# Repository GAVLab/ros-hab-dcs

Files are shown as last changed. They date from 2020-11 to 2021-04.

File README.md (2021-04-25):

# ros-hab-dcs

Robot Operating System (ROS) High Altitude Balloon (HAB) Data Collection System (DCS)

**Status:** Launched maiden flight

## Introduction

This is a system to collect a high altitude balloon dataset utilizing ROS for aerial navigation algorithmic development.  The datasets contain downward facing visual imagery, side-facing imagery, IMU, GPS, external barometric pressure, and internal and external temperature.  The system is designed to run Ubuntu Mate 20.04LTS with ROS Noetic Ninjemys on a Raspberry Pi 4 and an Arduino Nano.

## Installation

Please see the installation guide for how to setup the software packages and run the system: [documentation/INSTALLATION.md](documentation/INSTALLATION.md)

## Photos
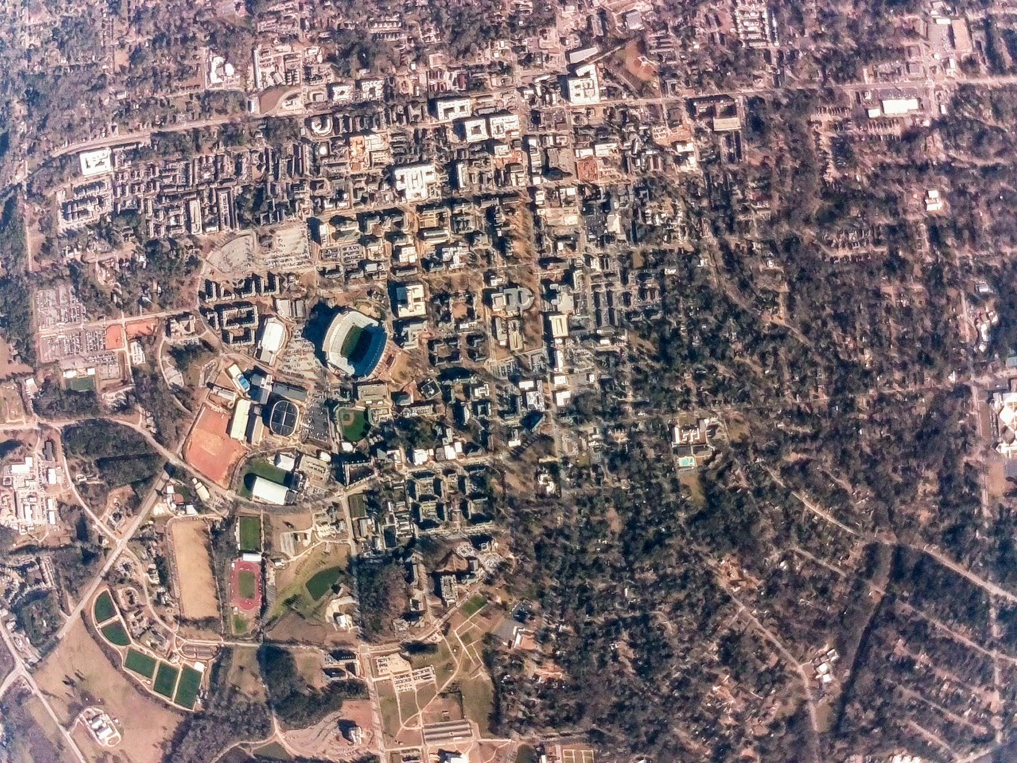
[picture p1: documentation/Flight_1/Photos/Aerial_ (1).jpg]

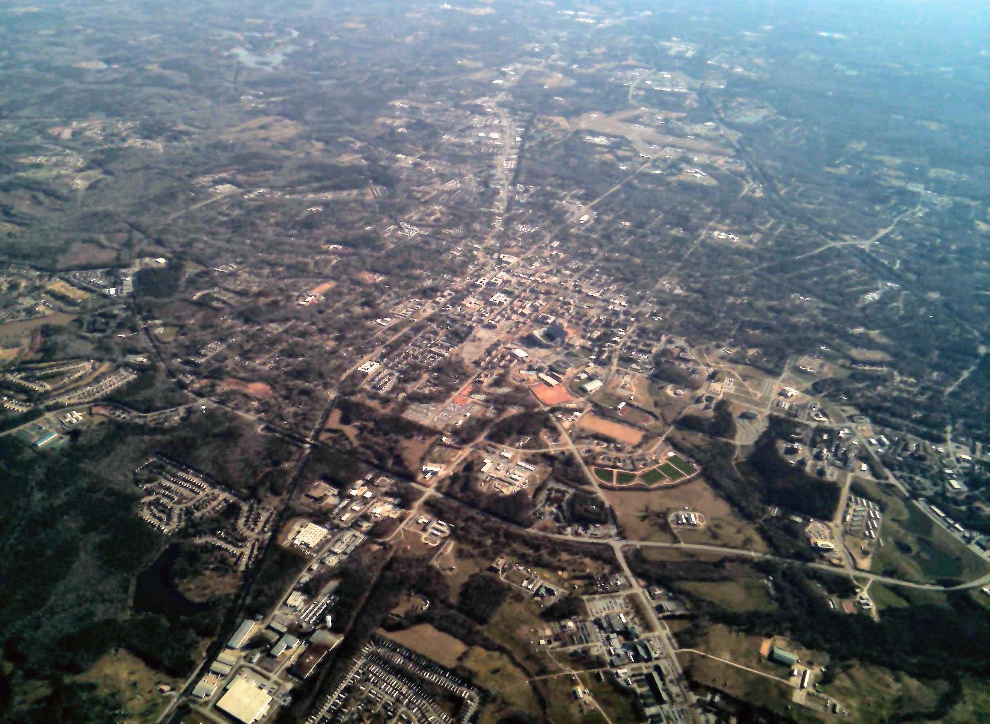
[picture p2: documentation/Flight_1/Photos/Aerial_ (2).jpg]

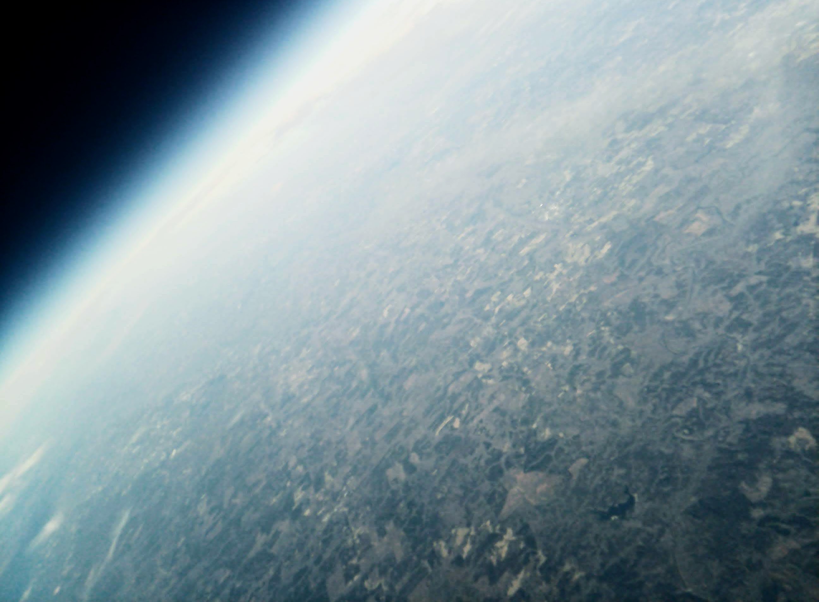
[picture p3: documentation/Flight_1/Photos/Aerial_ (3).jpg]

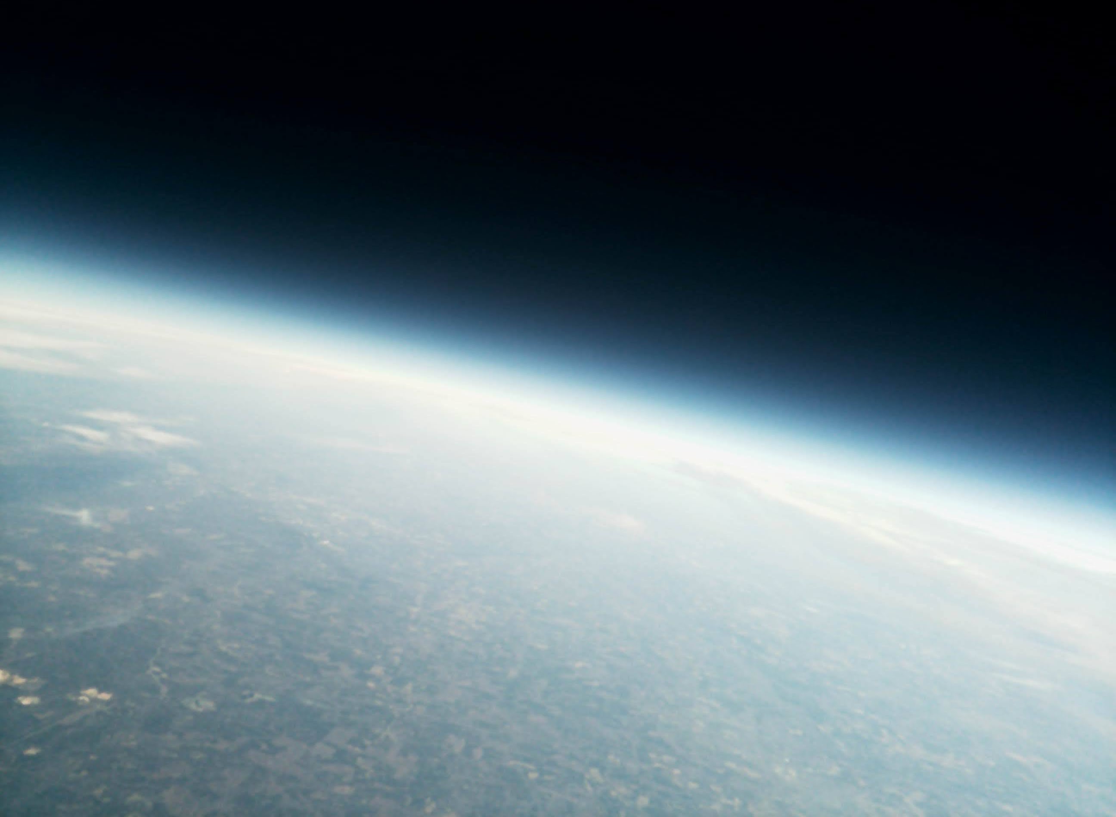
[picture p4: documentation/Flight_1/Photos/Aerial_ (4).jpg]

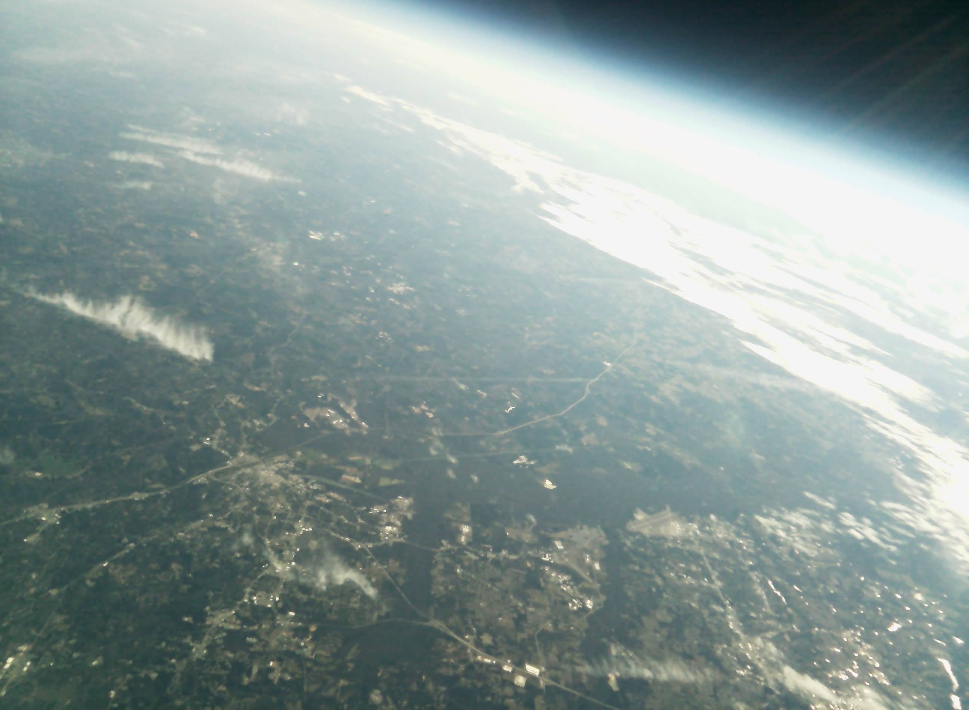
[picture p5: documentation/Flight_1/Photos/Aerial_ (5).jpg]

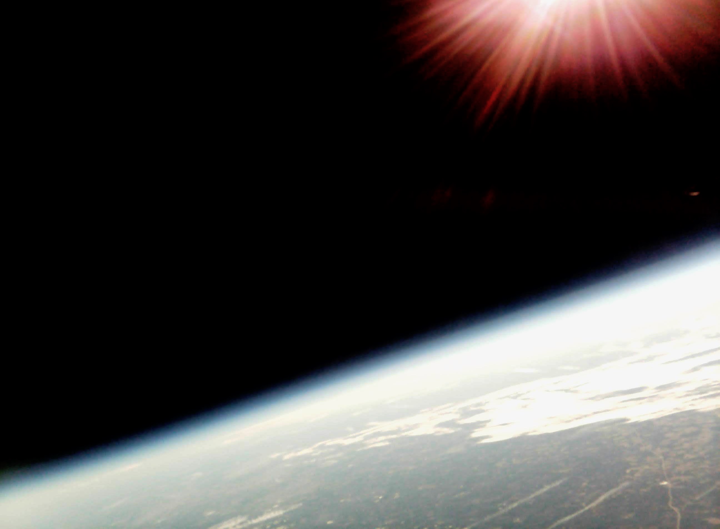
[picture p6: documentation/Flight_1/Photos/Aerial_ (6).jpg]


## Hardware

* SN01

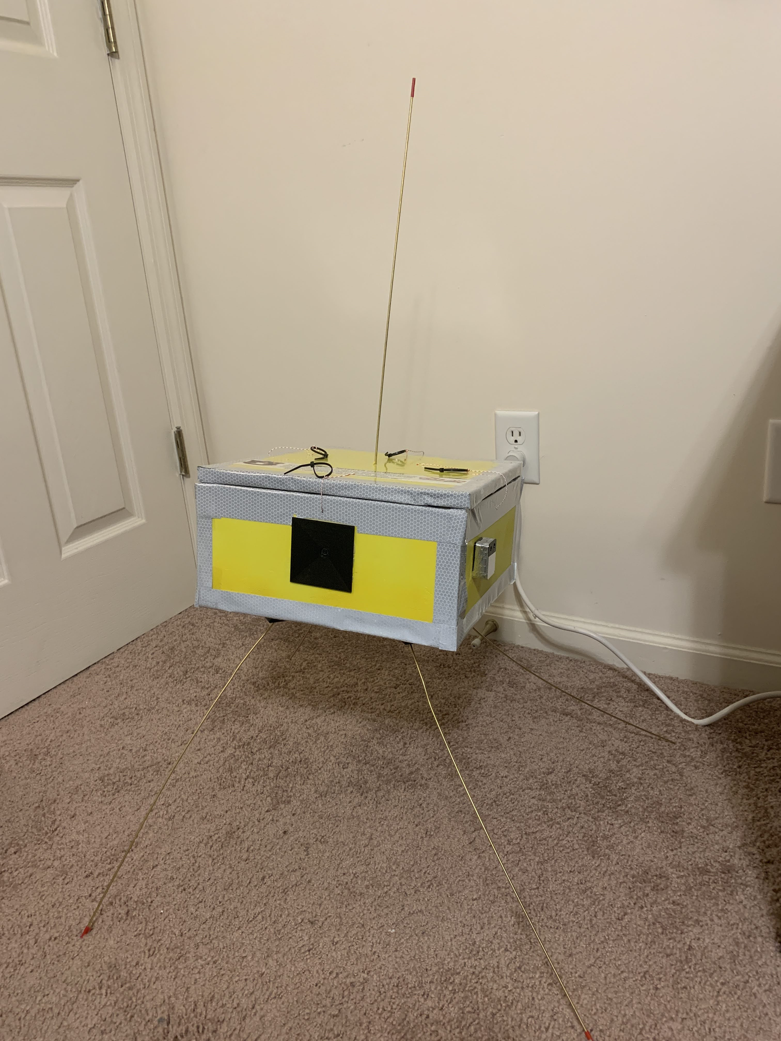
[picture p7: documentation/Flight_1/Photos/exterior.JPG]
     
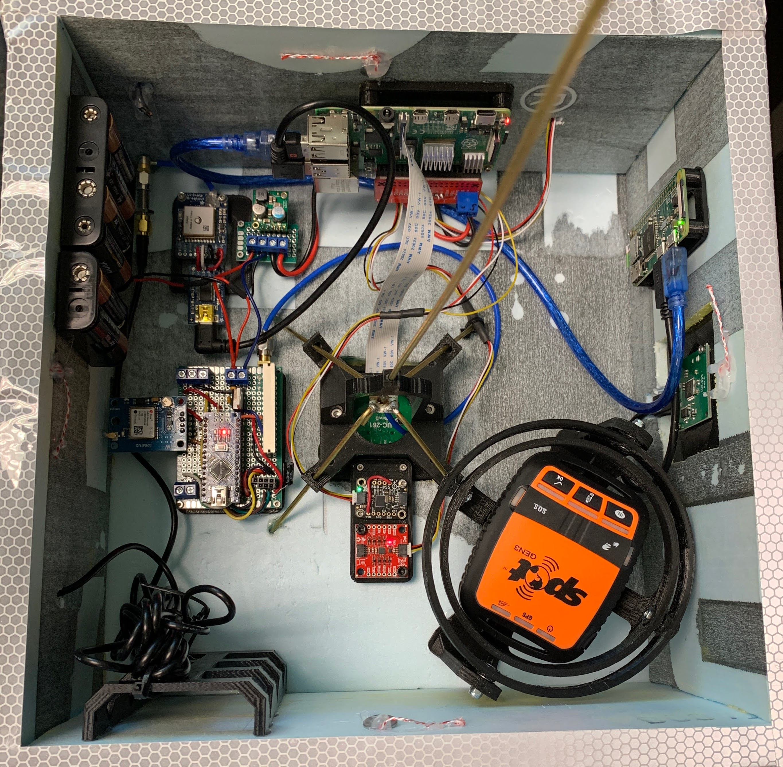
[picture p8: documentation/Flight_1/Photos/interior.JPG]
     
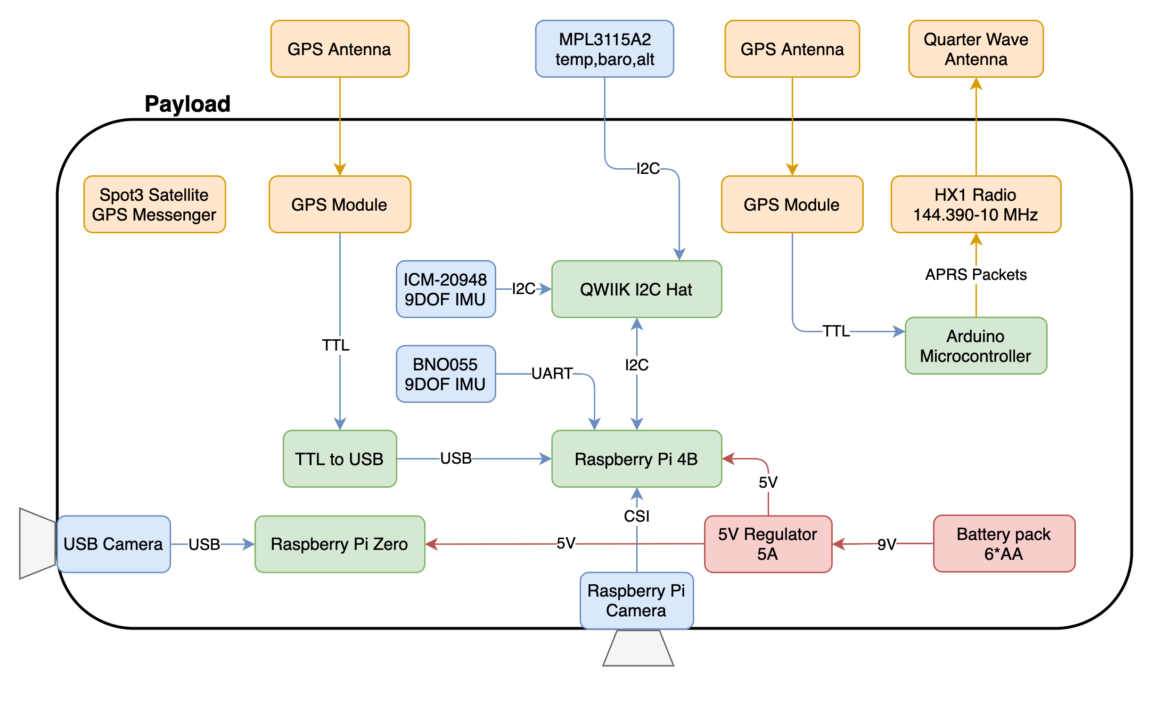
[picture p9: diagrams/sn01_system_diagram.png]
     
* SN02

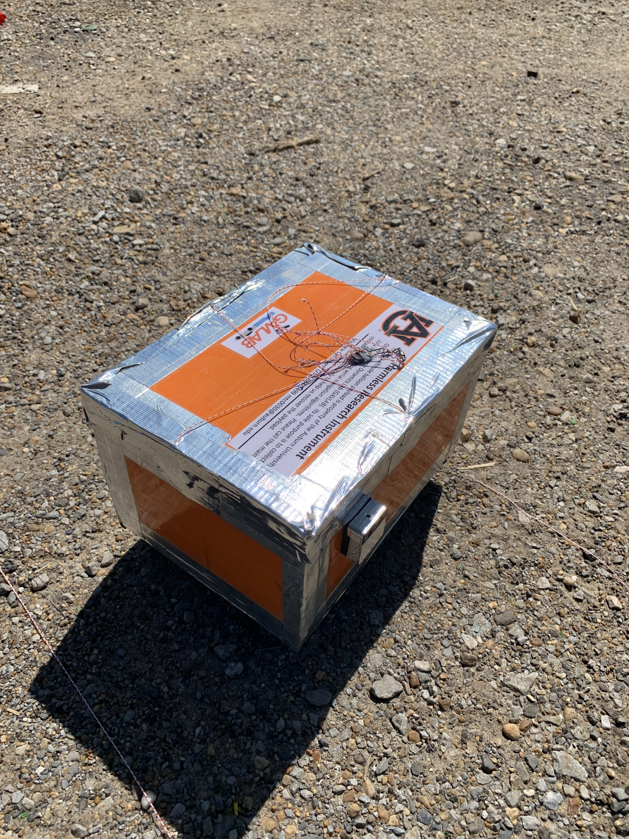
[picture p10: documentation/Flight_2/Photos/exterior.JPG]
     
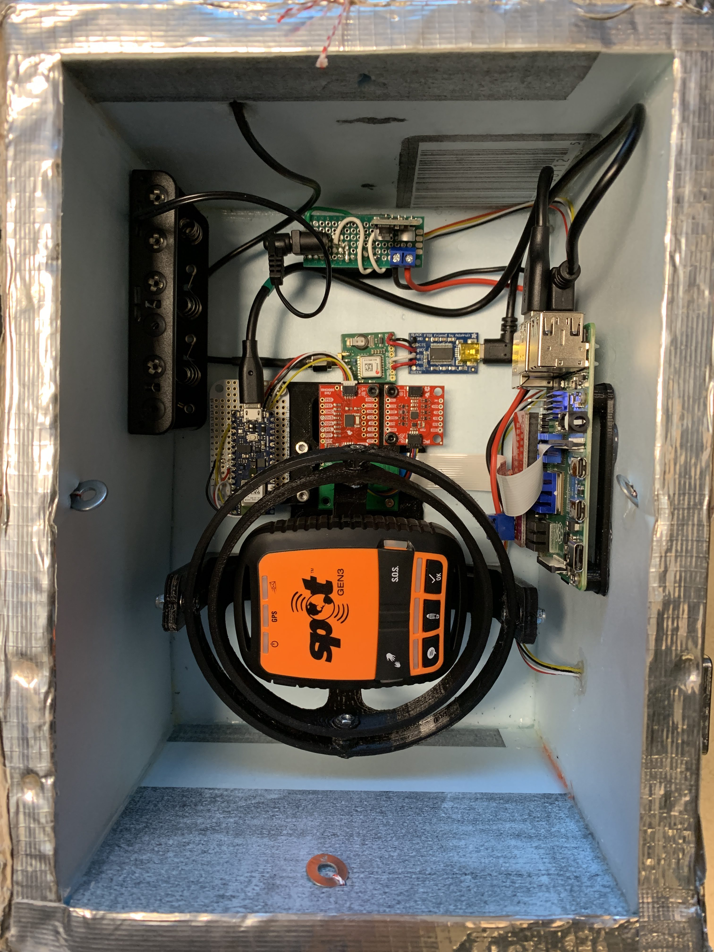
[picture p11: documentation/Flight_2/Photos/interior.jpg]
     
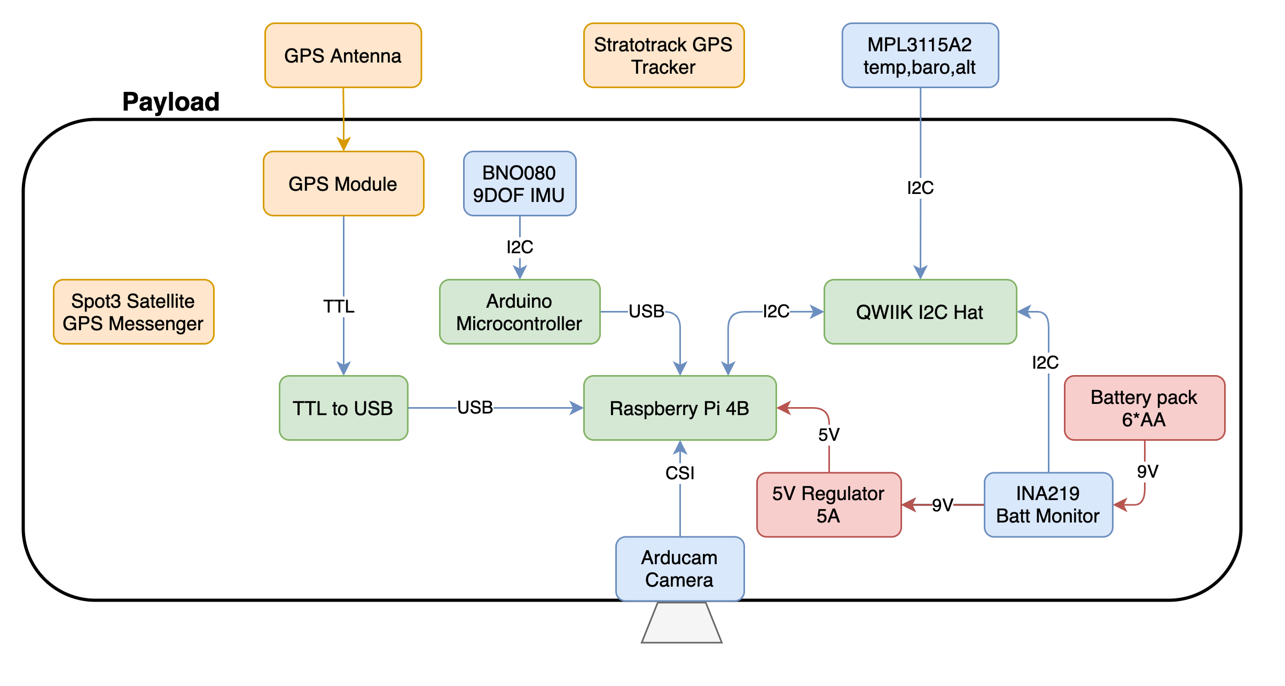
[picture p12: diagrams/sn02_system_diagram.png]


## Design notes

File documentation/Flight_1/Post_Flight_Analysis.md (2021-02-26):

# Post Flight Analysis - Flight 1 of SN01

## Launch

* **Date/Time:** 8:26am CST February 8th, 2021
* **Location:** 32.573700,-85.535900

## Flight
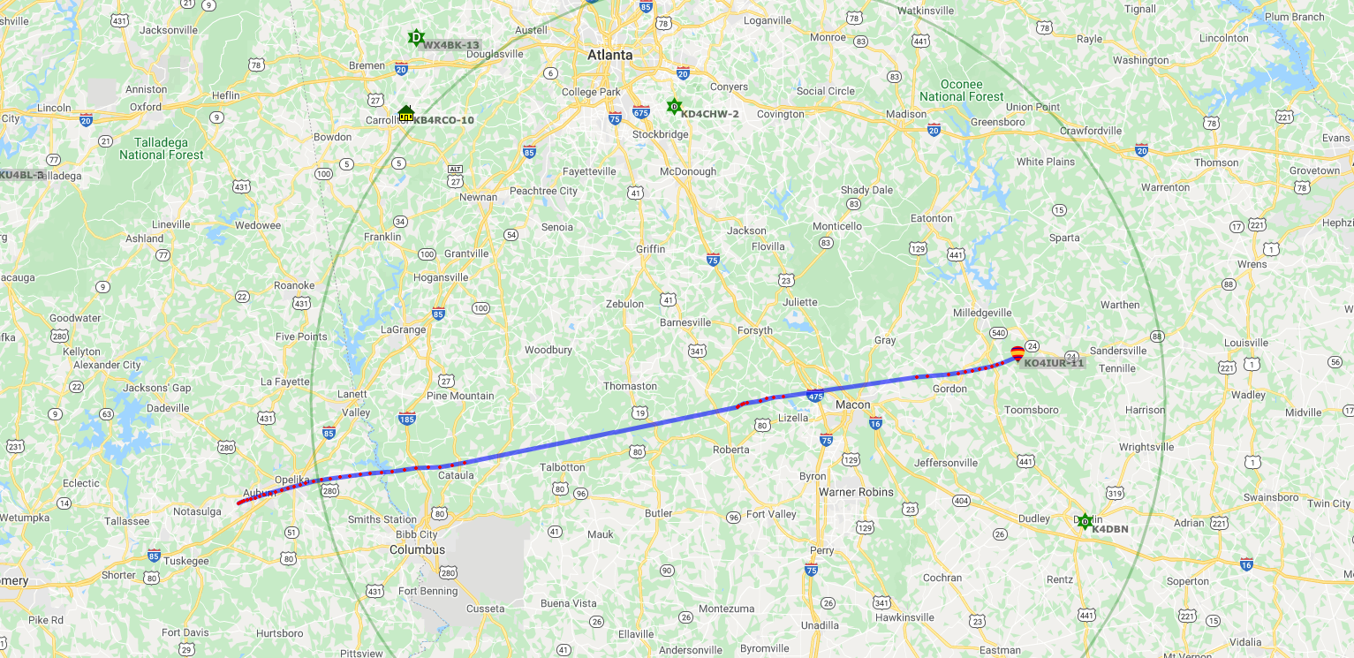
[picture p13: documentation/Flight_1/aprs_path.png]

* **Distance:** 142mi
* **Max Height:** TBD
* **Max Speed:** 140mph or 62.6m/s 

## Landing/Recovery
* **Landing Time:** 10:26am CST
* **Location**:  32.974091,-83.133568

### Attempt #1


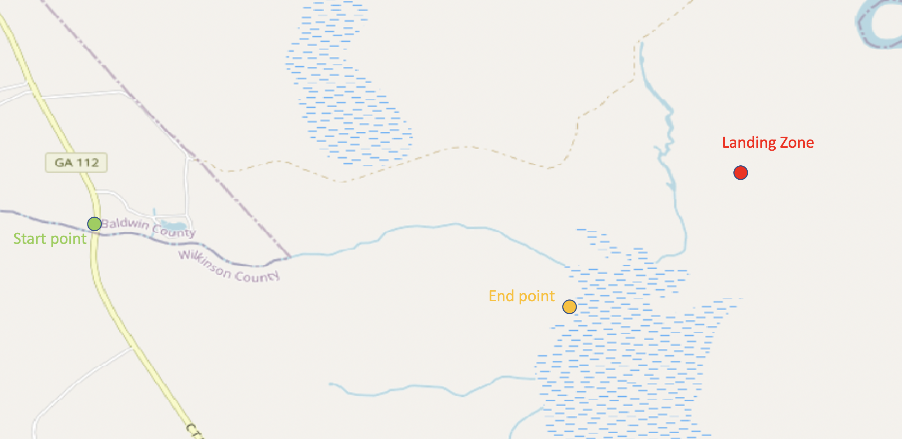
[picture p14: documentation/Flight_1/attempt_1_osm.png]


## Strengths (What went well)

* Balloon inflation process: Took about 1 hour including setup as expected.
* Sensor systems at launch: all systems were in a "norminal" state
* Weather conditions: good temperatures, low cloud cover, and decent ground speed winds (10mph)
* APRS Mobile tracking system:  received packets during most of flight when GPS was responding and payload was at a sufficiently high altitude.
* Spot Tracker gave multiple messages at the landing site for a few days

## Weaknesses (What went poorly)

* Landed in a densly forested swamp/hunting grounds.  Hard to get to.  Likely caught in a tree.
* No real good plan to extract payload from tree.
* APRS Tracking GPS cutout at 39,000ft.
* APRS antenna is bulky and hard to transport
* Payload stand is easy to tip as it is two cardboard boxes taped together.
* Balloon inflation measurement was hard to get accurate.
* Payload travelled 300 miles away.  Could be shorter if lower weight.
* File sizes were quite large.  128GB is too little storage.
* Radar reflector was heavy and time consuming to make.  Design could be improved.
* GPS uFL connector broke during week before flight.  Needs more caution when disconnecting it.
* We have no reliable data on battery current draw.

## Action items for next flight

* Recovery team should wear orange vests for safety especially if it landed on hunting grounds.
* Recovery team should have a ball shaped weight (duct tape aluminum foil ball) with fishing line attached to throw over branch balloon is caught on.
* Use different GPS sensor rated for higher altitude flight for APRS tracking system.  Share Adafruit Ultimate GPS with Pi by using Arduino Micro instead of Arduino Nano. Alternatively use stratotrack mounted above radar reflector: https://www.highaltitudescience.com/products/stratotrack-aprs-transmitter
* Use digital pull scale to improve balloon inflation precision
* Research ways to improve antenna design to something lighter weight and more robust
* Construct payload ground stand out of scrap wood
* Launch flight at location with more attention placed on where landing zone is.  Landing just west of Auburn might be better than landing far away from Auburn.
* Remove side camera system if launching on new platform
* Use 256GB sd card for Pi instead of 128GB SD card or reduce framerate of camera by half
* Handwarmer added extra weight.  A smaller box size with new antenna might reduce weight dramatically while still staying warm.
* Construct radar reflector out of cereal box to reduce weight.  Apply aluminum tape before assembling to reduce time and amount of tape used.
* Add i2c battery monitor sensor: https://www.adafruit.com/product/904
* Yellow exterior color is harder to see in forest.  Spray paint melts foam.  Bright orange is better.

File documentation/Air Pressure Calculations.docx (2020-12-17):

# Air Pressure Calculations

## Troposphere (<= 11km)

Assuming Pressure and Temperature at Mean Sea Level (MSL) are Known

h=(T_b)/(L_b)∙[(P/(P_b))^(-(R∙L_b)/(g_0 ∙M)) -1]

P=P_b ∙[1+(L_b)/(T_b)h]^((-g_0 ∙M)/(R∙L_b))

Where,

P_b =pressure at MSL [Pa]

T_b =temperature at MSL [K]

h=height above sea level [m]

L_b =tempature lapse rate [K/m]= -0.0065 [K/m]

R=universal gas constant=8.31432 [(N∙m)/(mol∙K)]

g_0 =gravitational acceleration constant=9.80665 [m/(s^2)]

M=molar mass of Earth^(') s air=0.0289644 [(kg)/(mol)]

Finding Pressure and Temperature at MSL with Temperature and Pressure at Known Height

T=L_b ∙h+T_b

Where,

T=measured temperature at h [K]

Deriving for T_b

T_b =T-L_b ∙h

Deriving for P_b

P_b =P/([1+(L_b)/(T_b)h]^((-g_0 ∙M)/(R∙L_b)))

## Stratosphere (> 11km and < 20km)

h=h_b +(R∙T_b ∙ln(P/(P_b)))/(-g_0 ∙M)

P=P_b ∙exp⁡[(-g_0 ∙M∙(h-h_b ))/(R∙T_b)]

Where,

P_b =pressure at the bottom of stratosphere= 22632 [Pa]

T_b =temperature at bottom of stratosphere= T_(b_(sea level)) -71.5 [K]

## References

https://www.mide.com/air-pressure-at-altitude-calculator

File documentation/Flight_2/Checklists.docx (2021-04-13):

# Flight Planning Checklist

- Select Date and Launch Time
  - Date: 4 / 12 / 2021
  - Time: 10:30 AM CST
- Weather Conditions (https://www.wunderground.com/forecast/us/al/auburn/32.62,-85.49)
  - Cloud cover < 50% : 6 %
  - Rain < 30% : 1 %
  - Jet Stream < 100 knots: 70 knots (https://weatherstreet.com/models/gfs-jetstream-wind-forecast.php)
  - Ground Speed Winds < 12 mph: 2mph
- Calculate Balloon Dynamics
  - Payload mass: 950 g
  - Balloon mass: 600 g
  - Positive lift: 875 g (http://tools.highaltitudescience.com/)
  - Total lift: 1825 g
  - Required helium: 87.18 cu-f (http://tools.highaltitudescience.com/)
  - Ascent Rate: 5.04 m/s (http://tools.highaltitudescience.com/)
  - Descent Rate: 7.1 m/s (https://www.highaltitudescience.com/products/0-9-m-parachute)
  - Burst Altitude: 27450 m
- Launch and Landing Location
  - Launch Address (https://www.freemaptools.com/elevation-finder.htm)

Uniontown Ball Park, Uniontown, AL 36786

Lat: 32.4519, Lon: -87.5074 Elev: 87.0m

    - Outside of restricted aerospace (https://skyvector.com/)
  - Predict landing zone (https://predict.habhub.org/)

Lat: 32.2346, Lon: -86.2678 Elev: 77m

- Flight Dynamics
  - Flight Time: 2 hrs, 2 min Landing Time: 1:32 PM
  - Total Distance: 73 mi
  - Driving distance (Launch to Recovery): 83 mi, Driving time: 1 hrs, 29 min
  - Driving distance (Round Trip): 283 mi, Driving time: 5 hrs, 0 min

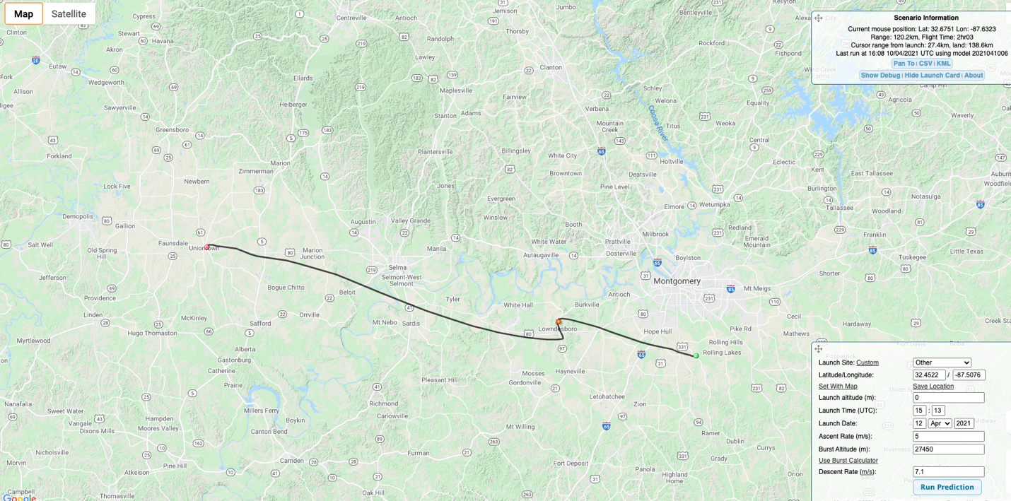
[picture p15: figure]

- File NOTEM: (http://blogs.und.edu/jdosas/wp-content/uploads/sites/108/2017/12/Instructions-Filing-a-NOTAM.pdf)
  - Call (877) 487-6867
  - Say “Hi, I would like to file a NOTAM for an Unmanned Balloon Flight”
  - Launch Location in Lat Lon with Degrees,Min,Second: (https://www.fcc.gov/media/radio/dms-decimal)
  - Lat: 32° 27' 6.84" Lon: -87° 30' 26.64"
  - Distance to nearest airport: 6.9 nmi
  - Atmosphere Level: Surface to Unlimited (appr 90,000ft)
  - Direction of flight: South-East
  - Time Effective:
    - 10:15am to 1:00pm CST or 1515 to 1800 Zulu on 4/12
  - My Initials: MTC (Mike Tango Charlie)
  - NOTEM Number: ZTL04/217 by GM
  - Filed Time: 11:48am on 4/10

# Departure Checklist

- Packed the following:
    - Balloon
    - Payload
    - Helium tank and inflator
    - Batteries
    - Toolbox
    - Wireless router
    - APRS receiver
- No USB mouse dongle receiver in Pi

# Pre-Flight Checklist

- Payload Preparation
- Identify tall obstacles: light posts, power lines, trees
- Identify wind direction (if applicable)
- Lay down tarp/blanket in location to maximize balloon travel distance to tall objects
- Setup router
- Remove lens cap
- Plug-in battery
- Connect via ssh
- Start ROS and verify sensors are working
- Calibrate IMUs
- Verify Spot3 is tracking
- Verify APRS signal is being transmitted via Direwolf
- Use duct tape to seal box
- Start recording ROS bag
- Balloon inflation (during payload preparation)
- Safety rope attached to payload and balloon from tank
- Balloon inflated to provide ______ g lifting force and tied off
- Take pictures of balloon inflation process
- Inspect train rope and knots
- Launch balloon
- Disengage safety rope from balloon
- Disengage safety rope from payload
- Record launch time ____:_____ _____
- Take video of launch process

# Post-Flight Checklist

- Upon Discovery of Payload
- Take picture of payload before touching and moving it
- Cut open box, disconnect battery
- Record landing site: Lat: ___________ Lon: ___________ Elev: __________
- Record recovery time ____:_____ _____

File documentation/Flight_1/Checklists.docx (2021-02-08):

# Flight Planning Checklist

- Select Date and Launch Time
  - Date: 2 / 8 / 2021
  - Time: 8:30 AM CST
- Weather Conditions (https://www.wunderground.com/forecast/us/al/auburn/32.62,-85.49)
  - Cloud cover < 50% : 40 %
  - Rain < 30% : 6 %
  - Jet Stream < 100 knots: 80 knots (https://weatherstreet.com/models/gfs-jetstream-wind-forecast.php)
  - Ground Speed Winds < 12 mph: 8mph E
- Calculate Balloon Dynamics
  - Payload mass: 1410 g
  - Balloon mass: 600 g
  - Positive lift: 1000 g (http://tools.highaltitudescience.com/)
  - Total lift: 2410 g
  - Required helium: 102.45 cu-f (http://tools.highaltitudescience.com/)
  - Ascent Rate: 5.1 m/s (http://tools.highaltitudescience.com/)
  - Descent Rate: 7.1 m/s (https://www.highaltitudescience.com/products/0-9-m-parachute)
  - Burst Altitude: 26390 m
- Launch and Landing Location
  - Launch Address (https://www.freemaptools.com/elevation-finder.htm)

Street: 2340 Wire Rd

City: Auburn State: AL Zip: 36832

Lat: 32.5737, Lon: -85.5358 Elev: 170m

    - Outside of restricted aerospace (https://skyvector.com/)
  - Predict landing zone (https://predict.habhub.org/)

Lat: 32.8543, Lon: -83.3750 Elev: 152m

- Flight Dynamics
  - Flight Time: 1 hrs, 56 min Landing Time: 10:26 AM
  - Total Distance: 127 mi
  - Driving distance (Launch to Recovery): 160 mi, Driving time: 2 hrs, 45 min
  - Driving distance (Round Trip): 319 mi, Driving time: 5 hrs, 49 min

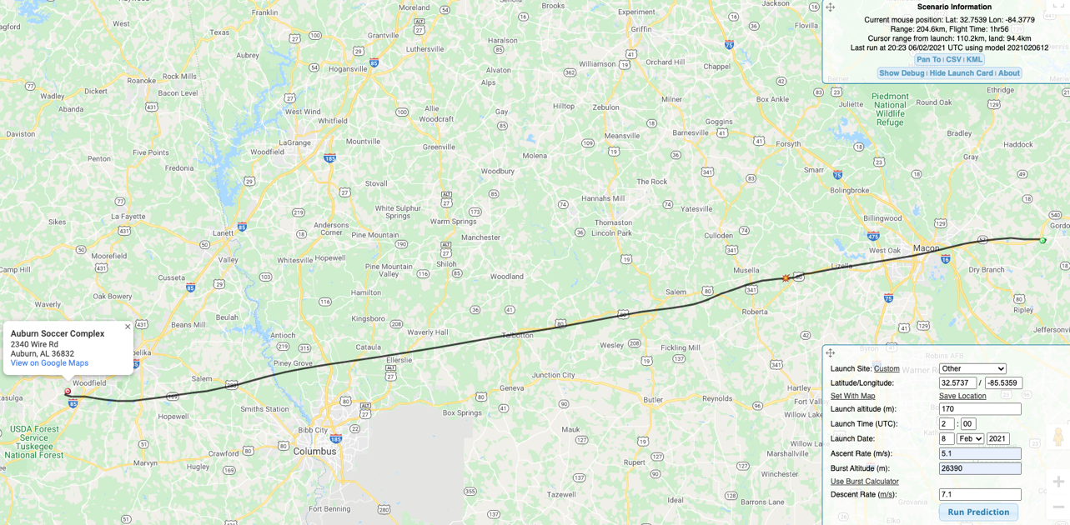
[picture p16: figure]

- File NOTEM: (http://blogs.und.edu/jdosas/wp-content/uploads/sites/108/2017/12/Instructions-Filing-a-NOTAM.pdf)
  - Call (877) 487-6867
  - Say “Hi, I would like to file a NOTAM for an Unmanned Balloon Flight
  - Launch Location in Lat Lon with Degrees,Min,Second: (https://www.fcc.gov/media/radio/dms-decimal)
  - Lat: 32° 34' 25" Lon: -85° 32' 08"
  - Distance to nearest airport:
  - Atmosphere Level: Surface to Unlimited (appr 90,000ft)
  - Direction of flight: East
  - Time Effective:
    - 8:30am to 11:30am CST or 1430 to 1730 Zulu on 2/8
  - My Initials: MTC (Mike Tango Charlie)
  - NOTEM Number: TGE02119
  - Filed Time: 3:00pm on 2/6

# Departure Checklist

- Packed the following:
    - Balloon
    - Payload
    - Helium tank and inflator
    - Extra batteries
    - Toolbox
    - Wireless router
    - APRS receiver
- No USB mouse receiver in Pi

# Pre-Flight Checklist

- Payload Preparation
- Identify tall obstacles: light posts, power lines, trees
- Identify wind direction (if applicable)
- Lay down tarp/blanket in location to maximize balloon travel distance to tall objects
- Start heating up hand warmer
- Setup router
- Plug-in battery
- Remove lens cap
- Connect via ssh
- Plugin BNO055 IMU
- Start ROS and verify sensors are working
- Calibrate IMUs (take all items out of pocket)
- Verify Spot3 is tracking
- Verify APRS signal is being transmitted via Direwolf
- Remove electrical tape from antennas
- Plug in Pi Zero power to start side camera recording
- Put hand warmer in box
- Use packing tape to seal box
- Start ROS bag
- Balloon inflation
- Safety rope attached to payload and balloon from tank
- Balloon inflated to provide ______ g lifting force and tied off
- Take pictures of balloon inflation process
- Inspect train rope and knots
- Launch balloon
- Disengage safety rope from balloon
- Disengage safety rope from payload
- Record launch time ____:_____ _____
- Take video of launch process

# Post-Flight Checklist

- Upon Discovery of Payload
- Take picture of payload before touching and moving it
- Cut open box, disconnect battery
- Record landing site: Lat: ___________ Lon: ___________ Elev: __________
- Record recovery time ____:_____ _____

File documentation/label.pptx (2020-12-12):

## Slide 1

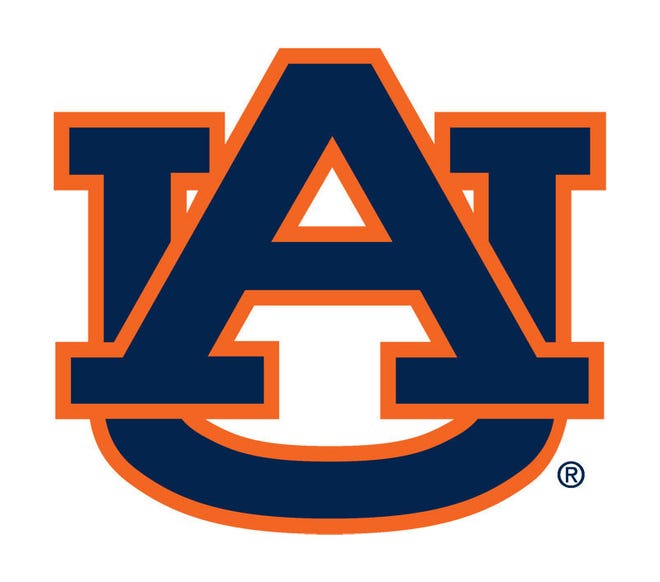
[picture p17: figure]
Does Auburn have a new logo? The university says no.

Harmless Research Instrument

This high altitude balloon payload is property of the Auburn University GPS and Vehicle Dynamics Lab (GAVLAB). Its sole purpose is to collect data for researching aerial navigation algorithms. Please call the main contact below immediately to help us recover the payload.

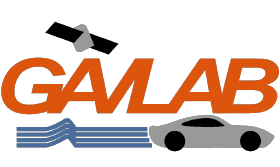
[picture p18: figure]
GAVLab · GitHub

Matthew Castleberry (256) 684-3499 mtc0030@auburn.edu

Harmless Research Instrument

This high altitude balloon payload is property of the Auburn University GPS and Vehicle Dynamics Lab (GAVLAB). Its sole purpose is to collect data for researching aerial navigation algorithms. Please call the main contact below immediately to help us recover the payload.

Matthew Castleberry (256) 684-3499 mtc0030@auburn.edu

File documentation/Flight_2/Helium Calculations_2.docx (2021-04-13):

Helium Calculations

Size Balloon: 600g

Payload weight: 950g

Positive lift: 1000g

Using this Calculator: https://www.highaltitudescience.com/pages/balloon-performance-calculator

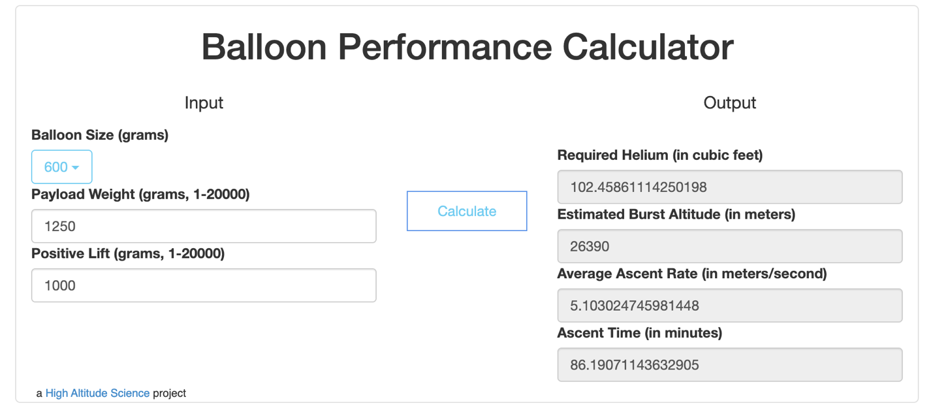
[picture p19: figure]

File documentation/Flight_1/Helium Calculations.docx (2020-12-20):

Helium Calculations

Size Balloon: 600g

Payload weight: 2.75lbs ~ 1250g

Positive lift: 1000g

Using this Calculator: https://www.highaltitudescience.com/pages/balloon-performance-calculator


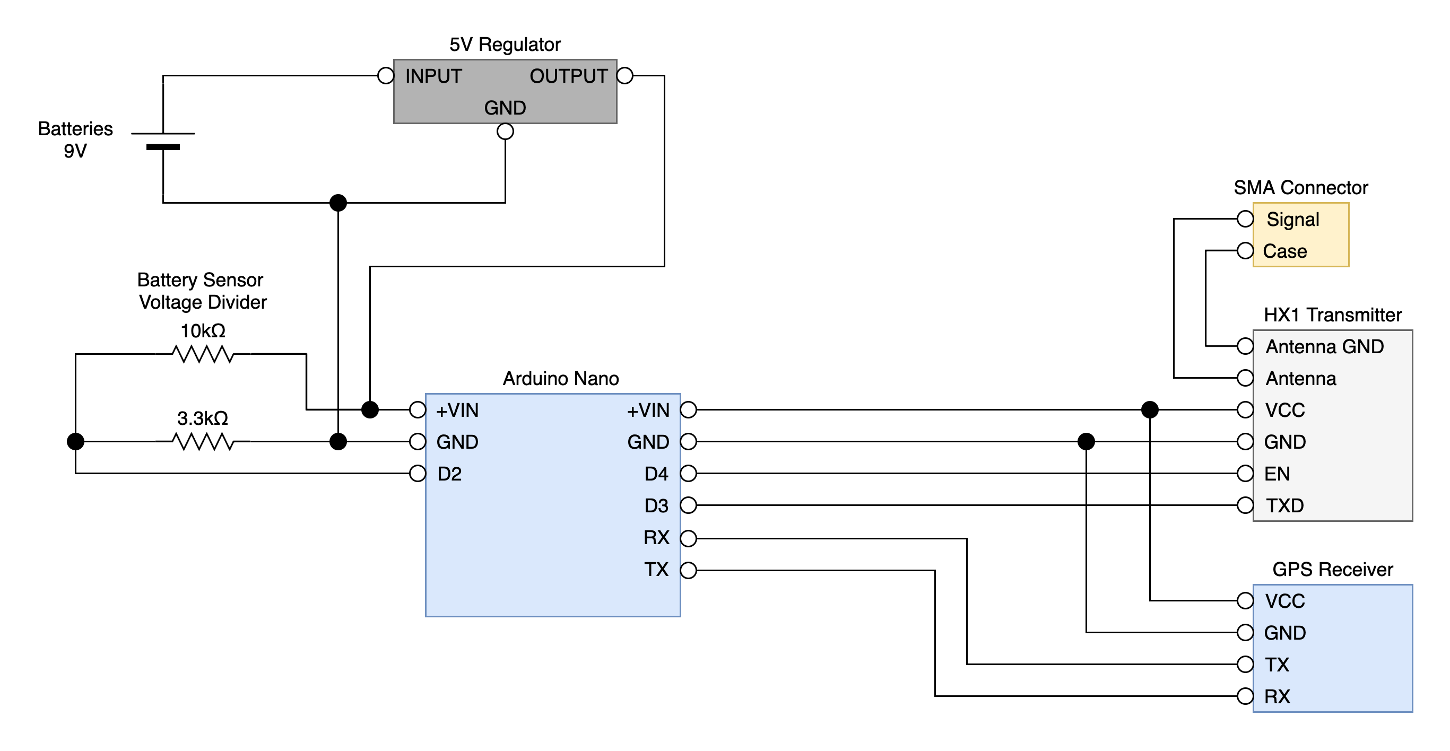
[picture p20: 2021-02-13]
diagrams/sn01_arduino_pinout_diagram.png

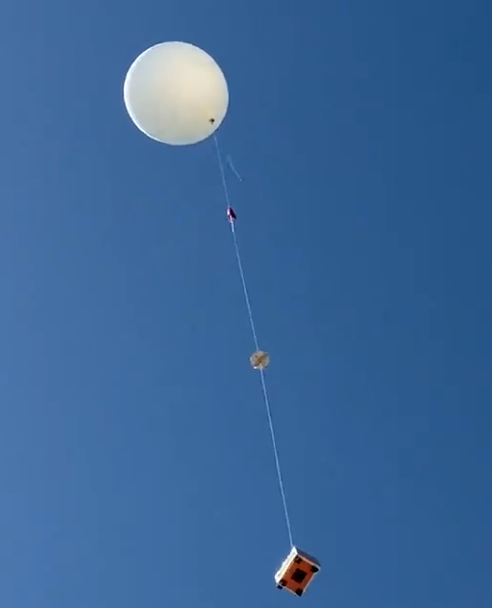
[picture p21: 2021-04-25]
documentation/Flight_2/Photos/launched.PNG

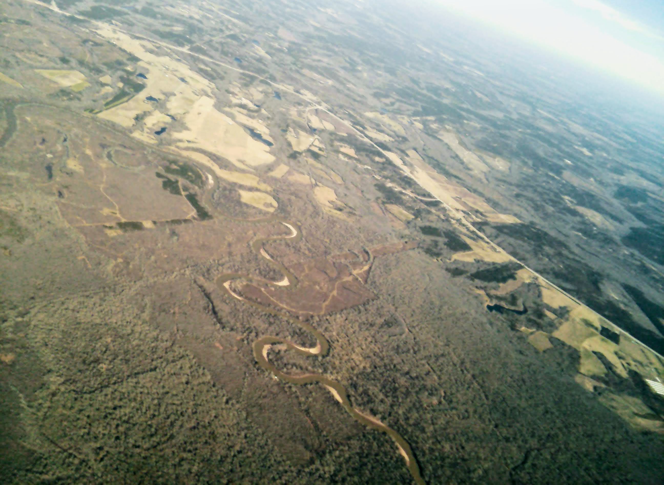
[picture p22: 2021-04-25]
documentation/Flight_1/Photos/Aerial_ (7).jpg

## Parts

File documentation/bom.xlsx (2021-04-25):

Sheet: Flight 1
Component | Subsystem | Name | Vendor | Price | Status | Fully Consumed in 1 Flight | ~ Payload Weight (g) | URL
Radar reflector | train | Cardboard | N/A | $0.00 | on payload | With Failure | 10
MicroSD * 2 | payload | 128GB micro SD | Amazon | $36.98 | on payload | With Failure | 0.25 | https://amz.run/3dZo
Raspberry Pi Cam Lens | payload | Lens Board for Raspberry Pi Camera | Amazon | $29.99 | on payload | With Failure | 30 | https://amz.run/3e6j
Secondary camera | payload | Arducam 8MP 1080P USB Camera V2 Module for Raspberry Pi | Amazon | $29.00 | on payload | With Failure | 5 | https://amz.run/3dZu
Arduino | payload | Arduino Nano | Digikey | $0.00 | on payload | With Failure | 5 | https://www.digikey.com/en/products/detail/dfrobot/DFR0010/6588448
Raspberry Pi I2C hat | payload | Qwiic / STEMMA QT HAT for Raspberry Pi | Digikey | $5.95 | on payload | With Failure | 10 | https://www.digikey.com/en/products/detail/DEV-14459/1568-1783-ND/7942481?itemSeq=342221022
Raspberry Pi | payload | Raspberry Pi 4B/2GB | Adafruit | $35.00 | on payload | With Failure | 20 | https://www.adafruit.com/product/4292
Regulator | payload | Pololu 5V, 5A Step-Down Voltage Regulator D24V50F5 | Amazon | $16.36 | on payload | With Failure | 5 | https://amz.run/43zy
IMU 1 | payload | 9-DOF Absolute Orientation IMU Fusion Breakout - BNO055 | Digikey | $19.95 | on payload | With Failure | 5 | https://www.digikey.com/en/products/detail/4646/1528-4646-ND/12609996?itemSeq=342221078
IMU 2 | payload | 9DOF IMU BREAKOUT - ICM-20948 | Digikey | $16.95 | on payload | With Failure | 5 | https://www.digikey.com/en/products/detail/sparkfun-electronics/SEN-15335/10279707
Barometer | payload | MPL3115A2 Barometric P/T/A Sensor | Adafruit | $0.00 | on payload | With Failure | 5 | https://www.adafruit.com/product/1893
Raspberry Pi | payload | Raspberry Pi Zero | Adafruit | $10.00 | on payload | With Failure | 15 | https://www.adafruit.com/product/3400
MicroUSB cable | payload | Micro USB to Micro USB OTG Cable, Male to Male | GovConnection | $4.07 | on payload | With Failure | 5 | https://www.govconnection.com/product/startech.com-micro-usb-to-micro-usb-m-m-adapter-cable-black-8/uuusbotg8in/31090379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
Primary GPS | payload | Ultimate GPS Breakout | Digikey | $39.99 | on payload | With Failure | 10 | https://www.digikey.com/en/products/detail/adafruit-industries-llc/746/5353613
Secondary GPS | payload | GY-NEO6MV2 NEO-6M GPS | Amazon | $0.00 | on payload | With Failure | 10 | https://amz.run/4IGH
GPS Antenna | payload | Waterproof GPS Active Antenna 28dB Gain | Amazon | $14.99 | on payload | With Failure | 20 | https://amz.run/43zu
Radio | payload | Radiometrix HX1 Radio Module | LEMOS | $60.49 | on payload | With Failure | 20 | https://lemosint.com/product/hx1-144-390-3/
Satellite GPS | payload | Spot 3 Satellite GPS Messenger | Amazon | $129.99 | on payload | With Failure | 114 | https://www.amazon.com/Spot-Satellite-GPS-Messenger-Orange/dp/B00C8S8S4W
Antenna Elements | payload | Ultra-Formable 260 Brss | McMasterCarr | $12.56 | on payload | With Failure | 15 | https://www.mcmaster.com/8859K166/
Antenna SMA Connector | payload | RF F Type Panel mount jack SMA | Digikey | $3.77 | on payload | With Failure | 5 | https://www.digikey.com/en/products/detail/adam-tech/RF2-155-T-00-50-G/9831203
Protoboard SMA Connector | payload | RF F Type Jack SMA | Digikey | $1.29 | on payload | With Failure | 5 | https://www.digikey.com/en/products/detail/adam-tech/RF2-04A-T-00-50-G/9830588
Reflective Tape | payload | Metallic Colored Duct Tape, Chrome, 1.88-Inch by 15 Yards | Amazon | $9.94 | on payload | With Failure | 5 | https://amz.run/4Jj9
Battery holder | payload | LAMPVPATH (Pack of 2) 4 AA Battery Holder | Amazon | $5.98 | on payload | With Failure | 13 | https://amz.run/3daO
Parachute | train | Near Space Parachute 1.0 m | High Altitude Science | $35.00 | consumed | Yes | 75 | https://www.highaltitudescience.com/products/0-9-m-parachute
Batteries | payload | Energizer AA Ultimate Lithium | Amazon | $15.98 | consumed | Yes | 138 | https://amz.run/3daM
Balloon | train | Weather Balloon 600g | High Altitude Science | $59.85 | consumed | Yes | 0 | https://www.highaltitudescience.com/products/600-g-near-space-balloon
Helium | train | Helium tank (estimated price) | AirGas | $80.00 | consumed | Yes | 0 | https://www.airgas.com/Gases/Helium/category/613
Satellite GPS subscription | payload | Flex Basic | FindMeSpot | $60.00 | On Hand | No | 0 | https://www.findmespot.com/en-us/products-services/service-plans
Protoboard Parts | payload | Universal PCB Board Kit | Amazon | $0.00 | On Hand | No | 10 | https://amz.run/43zq
JST cables | payload | 20 Sets Mini Micro Sh 1.0 Jst 4-Pin | Amazon | $7.99 | On Hand | No | 5 | https://amz.run/3g0X
Styrofoam box | payload | Polystyrene Foam | Lowes Pro | $12.96 | On Hand | No | 400 | https://www.lowes.com/pd/Dow-Common-0-55-in-x-4-ft-x-8-ft-Actual-0-55-in-x-4-ft-x-8-ft-RESIDENTIAL-SHEATHING-SQUARE-EDGE-1-R-3-Faced-Polystyrene-Garage-Door-F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
Hot Hand Warmers | payload | Tundras Hot Hand Warmers | Amazon | $13.99 | On Hand | No | 20 | https://amz.run/3dii
Inflator Tube | ground | weather balloon inflator | High Altitude Science | $85.00 | On Hand | No | 0 | https://www.highaltitudescience.com/products/3-cm-max-safe-inflator
String | train | emma kites 50Lbs 1000Ft Braided Dacron Polyester String | Amazon | $15.99 | On Hand | No | 10 | https://amz.run/3da4
Raspberry Pi Cable | ground | Raspberry Pi Power Supply 5.1V 3A with USB C | Adafruit | $7.95 | On Hand | No | 0 | https://www.adafruit.com/product/4298
Aluminum Foil Tape | train | 3M Aluminum Foil Tape 3381 | Amazon | $7.98 | On Hand | No | 15 | https://amz.run/3tIw
Cut-down Hot Wire | train | Resistance Wire Nichrome 80-22 AWG Gauge Spools 100 Feet | Amazon | $9.19 | On Hand | Unused | 5 | https://amz.run/3dkP
Sense Board | payload | Arduino Nano 33 BLE Sense | Digikey | $33.19 | On Hand | Unused | 10 | https://www.digikey.com/en/products/detail/arduino/ABX00031/10239970
Swivel hooks | train | Dr.Fish Fishing Barrel Swivel with Safety Snap | Amazon | $9.89 | On Hand | Unused | 10 | https://amz.run/3q4n
Relay module | payload | ICStation 1CH DC 3V 3.3V Relay Power Switch Module | Amazon | $11.99 | On Hand | Unused | 10 | https://amz.run/3jLR
Total |  |  |  | $950.20 |  |  | 550.25
 |  |  |  |  |  | Weight= | 1.213 | lbs
Component Type | Subtotals
payload | $483.25
consumed | $190.83
ground/bulk/unused | $276.12
Total | $950.20

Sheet: Flight 2
Component | Subsystem | Name | Vendor | Price | Status | Fully Consumed in 1 Flight | ~ Payload Weight (g) | URL
Radar reflector | train | Cardboard | N/A | $0.00 | consumed | With Failure | 10
MicroSD | payload | 256GB micro SD | Amazon | $32.99 | on payload | With Failure | 0.25 | https://amz.run/4Jir
Raspberry Pi Cam Lens | payload | Lens Board for Raspberry Pi Camera | Amazon | $27.99 | on payload | With Failure | 30 | https://amz.run/3e6j
Raspberry Pi I2C hat | payload | Qwiic / STEMMA QT HAT for Raspberry Pi | Amazon | $10.06 | on payload | With Failure | 10 | https://amz.run/4Jis
Raspberry Pi | payload | Raspberry Pi 4B/4GB | Digikey | $55.00 | on payload | With Failure | 20 | https://www.digikey.com/en/products/detail/raspberry-pi/RASPBERRY-PI-4B-4GB/10258781
Raspberry Pi Heatsinks | payload | Raspberry Pi Heatsinks | Amazon | $5.97 | on payload | With Failure | 5 | https://amz.run/4Jiw
Regulator | payload | Pololu 5V, 5A Step-Down Voltage Regulator D24V50F5 | Amazon | $14.30 | on payload | With Failure | 5 | https://amz.run/43zy
Power Monitor | payload | INA219 High Side DC Current Sensor Breakout | Adafruit | $9.95 | on payload | With Failure | 10 | https://www.adafruit.com/product/904
IMU (backup) | payload | 9-DOF Absolute Orientation IMU Fusion Breakout - BNO055 | Digikey | $19.95 | On Hand | With Failure | 5 | https://www.digikey.com/en/products/detail/4646/1528-4646-ND/12609996?itemSeq=342221078
IMU 1 | payload | SparkFun VR IMU Breakout - BNO080 | Sparkfun | $34.95 | on payload | With Failure | 10 | https://www.sparkfun.com/products/14686
IMU 2 | payload | 9DOF IMU BREAKOUT - ICM-20948 | Adafruit | $14.95 | on payload | With Failure | 5 | https://www.adafruit.com/product/4554
Barometer | payload | MPL3115A2 Barometric P/T/A Sensor | Digikey | $9.95 | on payload | With Failure | 5 | https://www.digikey.com/en/products/detail/adafruit-industries-llc/1893/4990783
Primary GPS | payload | Ultimate GPS Breakout USB | Digikey | $39.99 | on payload | With Failure | 10 | https://www.digikey.com/en/products/detail/adafruit-industries-llc/4279/10263862
GPS Antenna | payload | Waterproof GPS Active Antenna 28dB Gain | Amazon | $14.99 | on payload | With Failure | 20 | https://amz.run/43zu
Satellite GPS | payload | Spot 3 Satellite GPS Messenger | Amazon | $99.99 | on payload | With Failure | 87 | https://www.amazon.com/Spot-Satellite-GPS-Messenger-Orange/dp/B00C8S8S4W
Reflective Tape | payload | Chrome Duct Tape | Amazon | $10.59 | on payload | With Failure | 15 | https://amz.run/4KED
Battery holder | payload | Battery Holder 6X 1.5V AA Battery Storage | Digikey | $2.50 | on payload | With Failure | 20 | https://www.digikey.com/en/products/detail/dfrobot/FIT0141/7597083
Tracker | payload | stratotrack | High Altitude Science | $199.99 | consumed | With Failure | 30 | https://www.highaltitudescience.com/products/stratotrack-aprs-transmitter
Parachute | train | Near Space Parachute 1.0 m | High Altitude Science | $35.00 | On Hand | Yes | 75 | https://www.highaltitudescience.com/products/0-9-m-parachute
Batteries | payload | Energizer AA Ultimate Lithium (8 pack) | Amazon | $12.78 | consumed | Yes | 138 | https://amz.run/4KEO
Balloon | train | Weather Balloon 600g | High Altitude Science | $59.85 | consumed | Yes | 0 | https://www.highaltitudescience.com/products/600-g-near-space-balloon
Helium | train | Helium tank (estimated price) | AirGas | $80.00 | consumed | Yes | 0 | https://www.airgas.com/Gases/Helium/category/613
Pull scale | ground | HEETA Fish Scale with Backlit LCD Display | Amazon | $10.59 | On Hand | No | 0 | https://amz.run/4Jj2
Orange Vests | ground | SIFE High Visibility Reflective Safety Vest | Amazon | $24.86 | On Hand | No | 0 | https://amz.run/4Jj1
Satellite GPS subscription | payload | Flex Basic | FindMeSpot | $30.00 | consumed | No | 0 | https://www.findmespot.com/en-us/products-services/service-plans
Total |  |  |  | $857.19 |  |  | 510.25
 |  |  |  |  |  | Weight= | 1.125 | lbs
Component Type | Subtotals
payload | $604.11
consumed | $187.63
ground/bulk/unused | $65.45
Total | $857.19

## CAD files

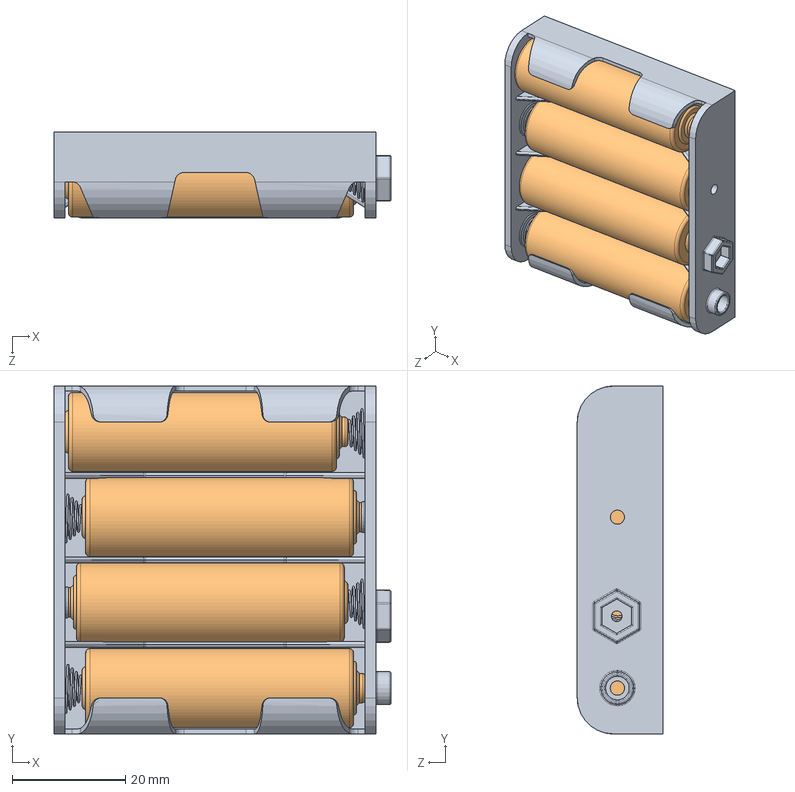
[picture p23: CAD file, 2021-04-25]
3D_Model/SN02/battery_holder/Batterie nel portabatterie.SLDASM
59.6 x 61.5 x 15.1 mm
User Library-R6_AA_UM3-1_5V_holder4AA
Batteria ricaricabile stilo x 4

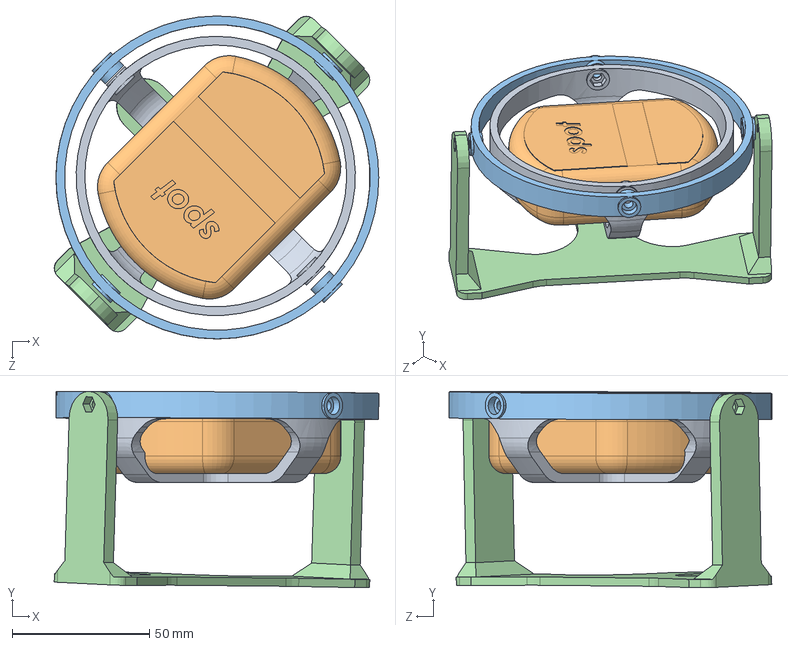
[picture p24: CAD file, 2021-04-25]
3D_Model/SN02/gyro.SLDASM
118.1 x 71.4 x 117.5 mm
gyro_inner
SPOT3
gyro_middle
gyro_outer

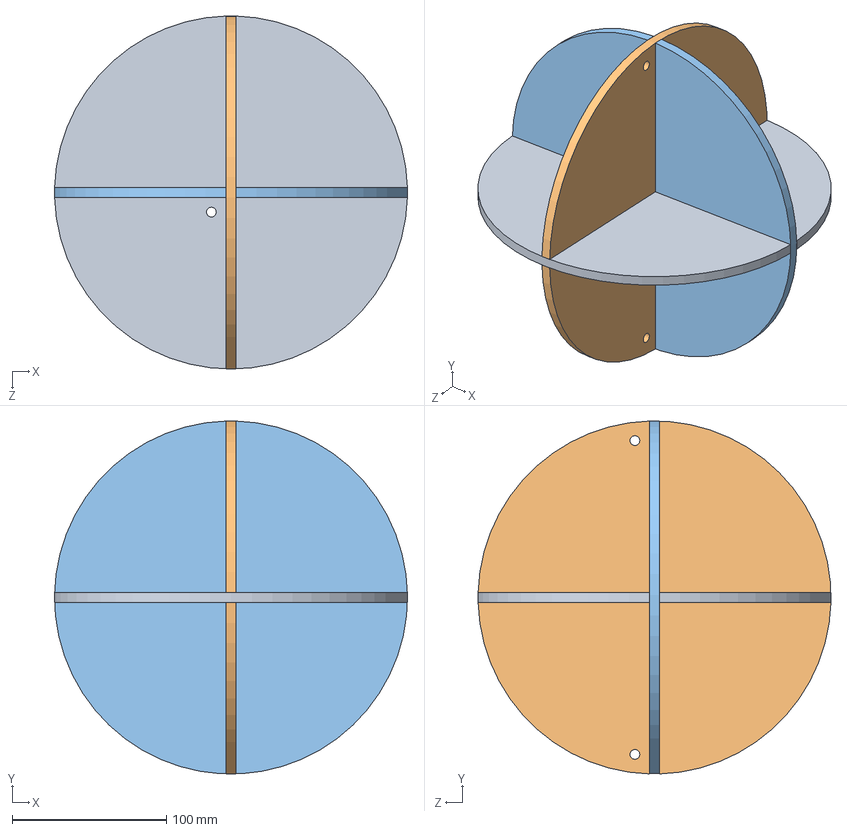
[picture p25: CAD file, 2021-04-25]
3D_Model/SN01/radar_reflector.SLDASM
228.6 x 228.5 x 228.6 mm
radar_reflector_B
radar_reflector_A
radar_reflector_C

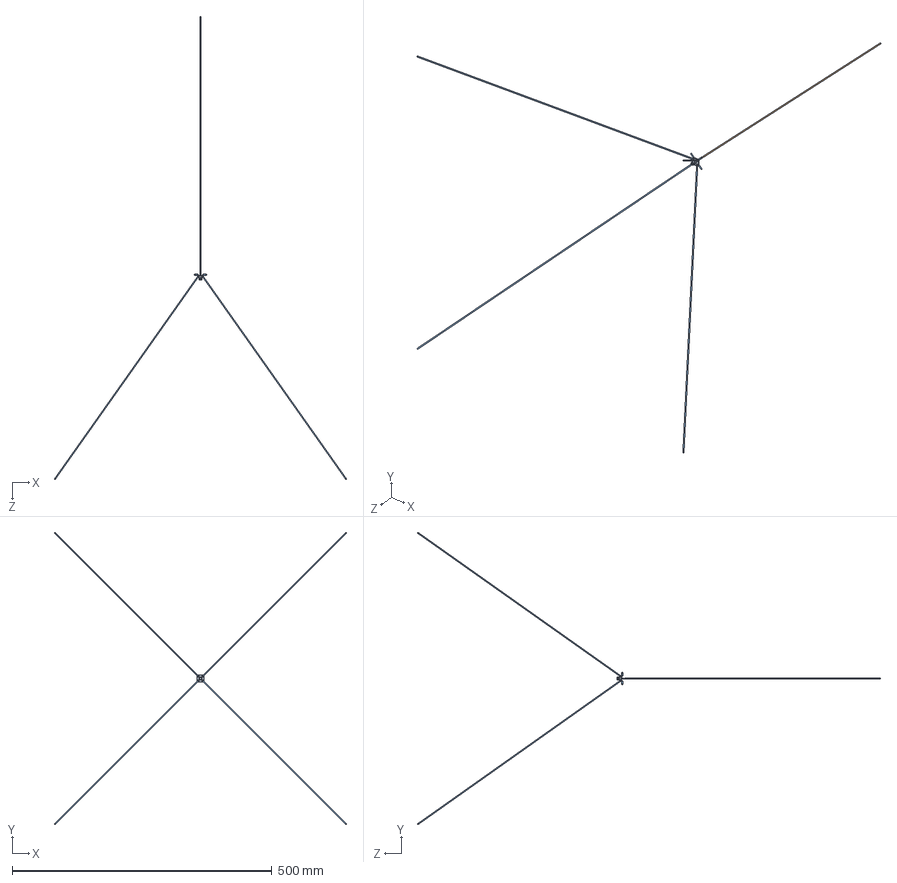
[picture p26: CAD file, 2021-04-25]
3D_Model/SN01/quarter_wave_antenna.SLDASM
563.0 x 563.0 x 892.1 mm
sma_panel_mount
quarter_wave_monopole
quarter_wave_radial x 4

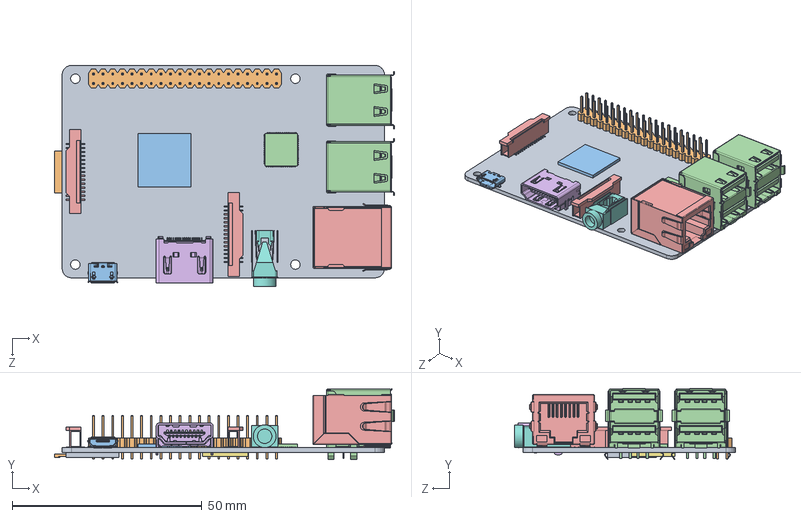
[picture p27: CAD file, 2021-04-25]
3D_Model/SN01/RaspberryPi2 model B SW.SLDASM
89.6 x 18.7 x 58.3 mm
Mainboard2
GPIO
Processor
GPU
CameraAssembly x 2
hdmi
RAM
Audio
MicroSDSocket
MicroSD
micro USB2
usb double x 2
RJ45-LED

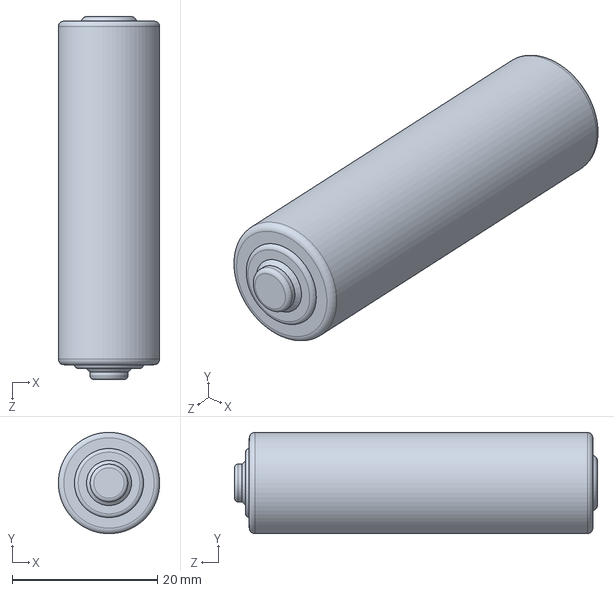
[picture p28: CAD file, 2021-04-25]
3D_Model/SN01/battery_holder/Batteria ricaricabile stilo.SLDPRT
14.0 x 14.0 x 50.0 mm

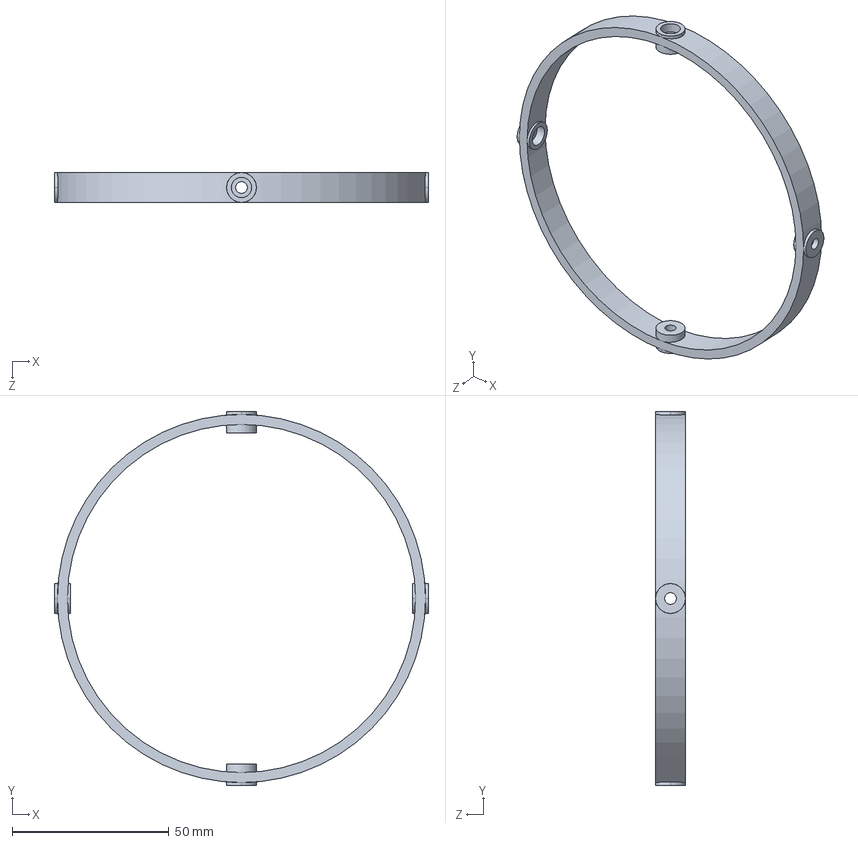
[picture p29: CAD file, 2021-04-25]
3D_Model/SN01/gyro_middle.SLDPRT
119.4 x 119.4 x 9.53 mm

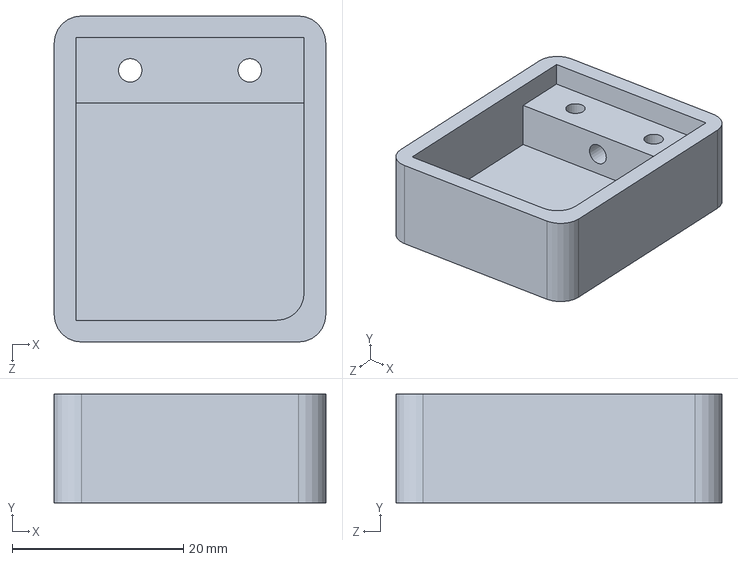
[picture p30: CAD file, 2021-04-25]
3D_Model/SN02/mpl3115a2_altimeter_cover.SLDPRT
31.8 x 12.7 x 38.1 mm

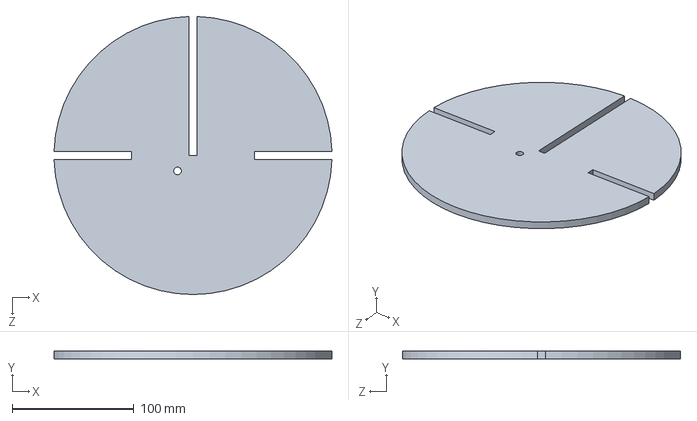
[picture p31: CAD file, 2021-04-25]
3D_Model/SN01/radar_reflector_B.SLDPRT
228.5 x 6.35 x 228.6 mm

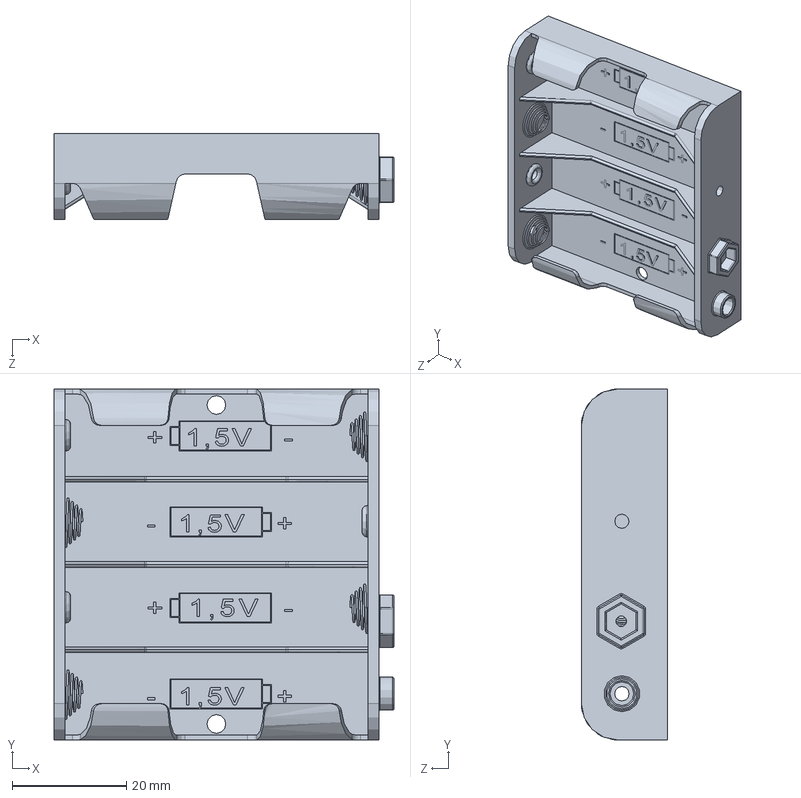
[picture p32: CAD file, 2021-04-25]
3D_Model/SN02/battery_holder/User Library-R6_AA_UM3-1_5V_holder4AA.SLDPRT
59.6 x 61.5 x 15.1 mm

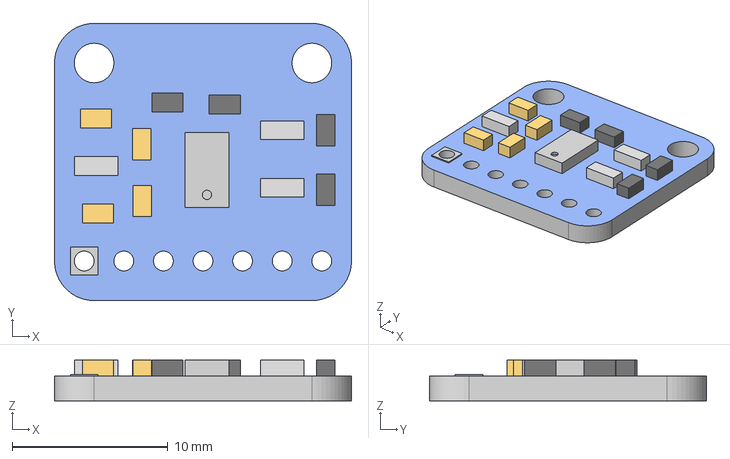
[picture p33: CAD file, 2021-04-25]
3D_Model/SN02/mpl3115a2_altimeter.step
19.1 x 17.8 x 2.60 mm

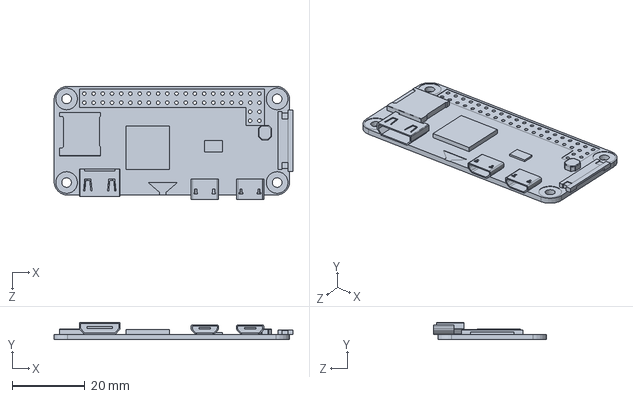
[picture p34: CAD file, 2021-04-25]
3D_Model/SN01/RaspberryPiZeroW.SLDPRT
65.9 x 4.80 x 31.2 mm

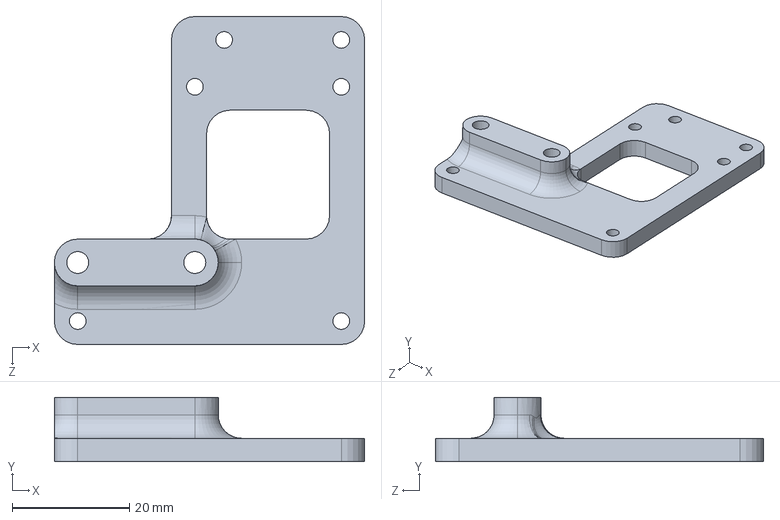
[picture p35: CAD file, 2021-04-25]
3D_Model/SN02/imu_arduino_holder.SLDPRT
53.0 x 11.0 x 56.0 mm

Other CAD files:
3D_Model/SN02/RaspberryPi2 model B SW.SLDASM
3D_Model/SN01/12pin-header.SLDPRT
3D_Model/SN01/12pin-header.stp
3D_Model/SN01/40Pin.SLDPRT
3D_Model/SN01/40Pin.STEP
3D_Model/SN01/SPOT3.SLDPRT
3D_Model/SN01/antenna_bracer.SLDPRT
3D_Model/SN01/antenna_holder_middle.SLDPRT
3D_Model/SN01/antenna_holder_top.SLDPRT
3D_Model/SN01/arducam_csi.SLDPRT
3D_Model/SN01/arducam_csi_holder.SLDPRT
3D_Model/SN01/arducam_usb.SLDPRT
3D_Model/SN01/arducam_usb_holder.SLDPRT
3D_Model/SN01/battery_holder/1_5V_holder4AA.x_t
3D_Model/SN01/battery_holder/Batteria ricaricabile stilo.x_t
3D_Model/SN01/bno055_imu.SLDPRT
3D_Model/SN01/cutdown_system.SLDPRT
3D_Model/SN01/drawings/payload_bottom.SLDDRW
3D_Model/SN01/drawings/payload_left.SLDDRW
3D_Model/SN01/drawings/radar_reflector_A.SLDDRW
3D_Model/SN01/drawings/radar_reflector_B.SLDDRW
3D_Model/SN01/drawings/radar_reflector_C.SLDDRW
3D_Model/SN01/feather_sense.SLDASM
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

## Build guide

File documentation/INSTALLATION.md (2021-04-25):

# Installation

## Installation Instructions

### Set Up the Pi (Basics)

* Download and flash microSD with Ubuntu Mate 20.04 Raspberry Pi 64-bit
* Connect to AU_WiFi (if on Auburn University's network): http://www.eng.auburn.edu/admin/ens/helpdesk/on-campus/wireless.html

### Clone repository and get submodules

```bash
git clone https://github.com/GAVLab/ros-hab-dcs --recursive
```

If you are having trouble with submodules try the following commands

```bash
git submodule update --init --recursive
```

### Set Up VNC on the Pi (Optional)

* Install ifconfig and x11vnc: `sudo apt-get install net-tools x11vnc`
* Run `ifconfig` to identify ip address.
* Start the VNC

  ```bash
    startx &
    x11vnc &
  ```

* Login to VNC viewer with IP address
  
### Install ROS and other Basics

 * Install ROS Noetic with this tutorial: http://wiki.ros.org/noetic/Installation/Ubuntu
 * ROS Desktop (not full) is sufficient.
 * Add repository to .bashrc
 ```
 echo "source ~/ros-hab-dcs/catkin_ws/devel/setup.bash" >> ~/.bashrc
 source ~/.bashrc
 ```
 * Install Python 3
 ```
 sudo apt-get install python3
 ```
 * Install various Python libraries
 ```
 pip3 install scipy
 ```

### Fix raspi_cpu_temp node
* Open `~/ros-hab-dcs/catkin_ws/src/raspi_cpu_temp/scripts/raspi_cpu_temp_node.py`
* Change first line to `#!/usr/bin/env python3`
  
### Setup i2c on Pi

* Enable i2c
  
  ```bash
  sudo apt-get install i2c-tools
  i2cdetect -l
  ```

* Add `i2c-devl` to boot with `sudo nano /etc/modules-load.d/modules.conf`
* Slow down baud rate by adding `dtparam=i2c_baudrate=10000` with `sudo nano /boot/firmware/usercfg.txt`
* Install wiringpi `sudo apt install wiringpi`
* Ensure proper permissions to prevent i/o errors: 
```
cd /dev
sudo chmod og+rwx gpio*
```
* Connect i2c devices to Sparkfun Qwiic hat and run `i2cdetect -y 1` to identify channels
* Install Circuit Python: https://learn.adafruit.com/circuitpython-on-raspberrypi-linux/installing-circuitpython-on-raspberry-pi
* Install driver for various sensors: `sudo pip3 install adafruit-circuitpython-bno055 adafruit-circuitpython-mpl3115a2 sparkfun-qwiic-icm20948 adafruit-circuitpython-ina219` 

### Setup UART  on Pi
* Follow the instructions found here: https://raspberrypi.stackexchange.com/questions/114366/rpi4-serial-port-not-working-on-either-raspberry-os-or-ubuntu
* Enable UART Permissions
```bash
sudo adduser $USER tty
sudo adduser $USER dialout 
sudo chmod g+r /dev/ttyAMA0
sudo chmod g+r /dev/ttyUSB0
```

### Setup the GPS

* Install ROS ublox: `sudo apt install ros-noetic-ublox`

### Setup Camera

* ROS Libraries

```bash
sudo apt-get install -y ros-noetic-camera-info-manager ros-noetic-rqt-image-view ros-noetic-compressed-image-transport ros-noetic-dynamic-reconfigure ros-noetic-usb-cam
```

* Enable CSI Camera
  ```sudo modprobe bcm2835-v4l2```
* Check video ports
  ```v4l2-ctl --list-devices```
* View Results once Running Node
  ```rqt_image_view```
* Setup library for camera calibration
  ```sudo apt-get install ros-noetic-image-geometry```
* Perform camera calibration. Move checkerboard paper until all bars are green and press "Calibrate" wait until results are printed to terminal (may take up to 10 minutes).  Press save (may take up to 5 minutes).  Press commit.

```bash
roslaunch ~/ros-hab-dcs/launches/sensors/camera_calib.launch
rosrun camera_calibration cameracalibrator.py --size 9x6 --square 0.022 image:=/down_cam/image_raw camera:=/down_cam
```

## Running system

```bash
cd  ~/ros-hab-dcs/launches/
roslaunch full_flight.launch
./record_full.sh
```

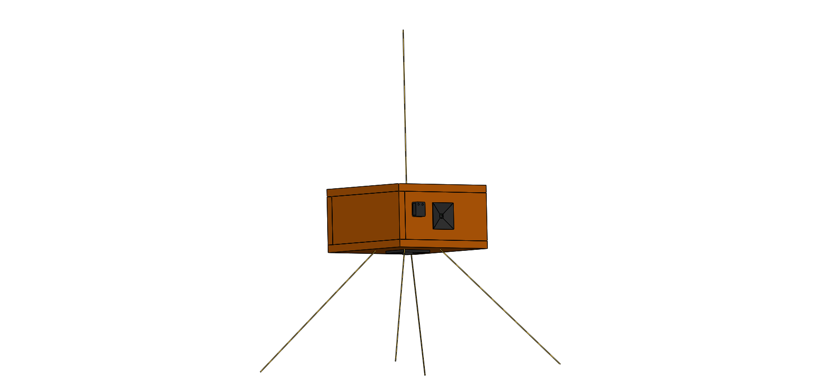
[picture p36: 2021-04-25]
3D_Model/SN01/images/payload_assembly.PNG

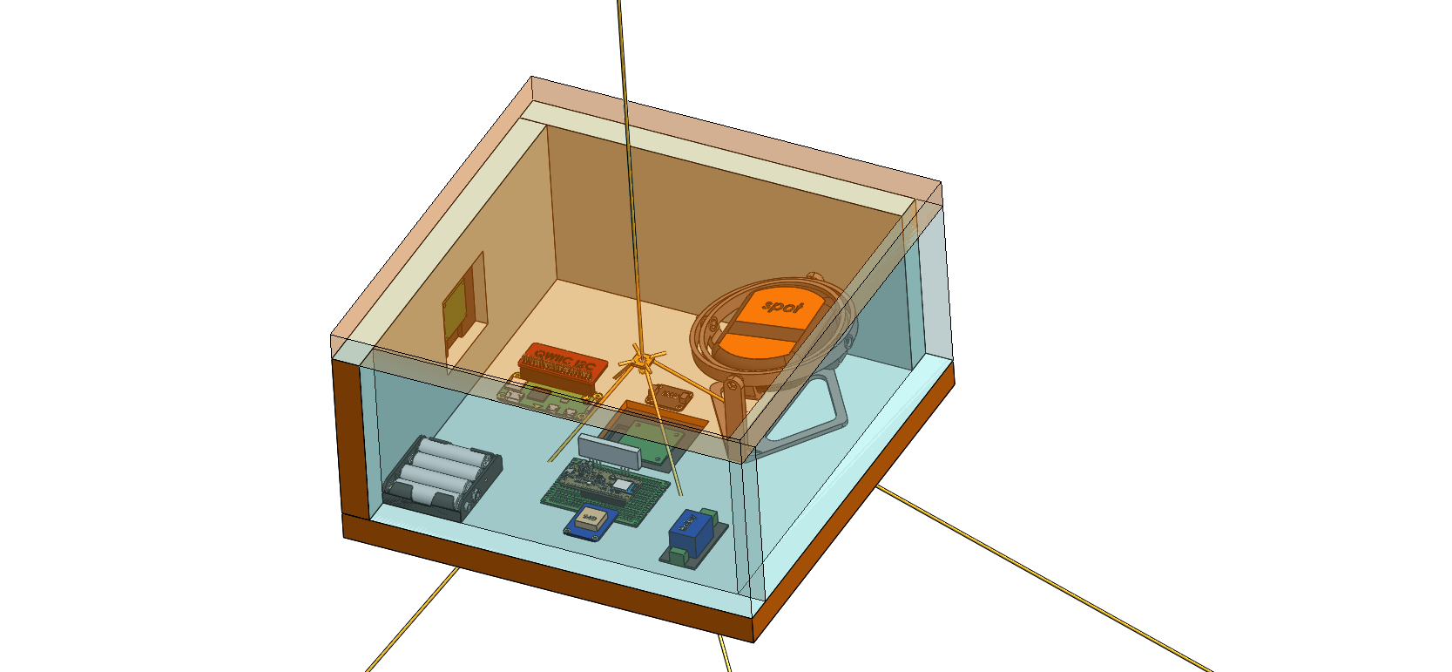
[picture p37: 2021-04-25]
3D_Model/SN01/images/payload_assembly_internals.PNG

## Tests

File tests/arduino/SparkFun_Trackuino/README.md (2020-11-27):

Banner

This is the firmware for Trackuino, an open-source APRS tracker based on the Arduino platform. It was designed primarily to track high altitude balloons, so it has other handy features like reading temperature sensors and a buzzer for acoustic location.

Trackuino is intended for use by licensed radio amateurs.

Features
========

 * Arduino shield form factor (you can stack more shields on it)
 * GPS: Venus 638FLPx. Reports okay above 18 Km.
 * Radio: Radiometrix's HX1 (300 mW).
 * 1200 bauds AFSK using 8-bit PWM
 * Sends out standard APRS position messages (latitude, longitude, altitude, course, speed and time).
 * Internal/external temperature sensors (LM60) to read temperature in and outside the payload
 * Active/passive buzzer support to ease acoustic payload location.
 * 2 x SMA female plugs (1 x GPS in + 1 x radio out)
 * Open source (GPLv2 license), both software and hardware. In other words, do whatever you want with it: modify it, add it to your project, etc. as long as you opensource your modifications as well.

Download
========

The latest version is 1.52.

Use the `Download ZIP` button to get the source code.

Building
========

If you are building for the Arduino platform you need Arduino IDE version 0023 or higher (tested with versions 0023, 1.0.x and 1.5.x). Get it from the [Arduino web site](http://arduino.cc/).

If you are building for the Chipkit Uno32 you need the Mpide IDE. Tested with 0023-20130715. Get it from the [Chipkit site](http://chipkit.net/).

Unzip the firmware in your sketches directory and load it up by double-clicking on trackuino.ino.

The single most important configuration file is "config.h". The file is self-documented. Here is where you set up your callsign, among other things.

Flashing
========

**Important**: When flashing the Arduino/Uno32, remove the Venus GPS or the entire Trackuino shield. After flashing the firmware, you can plug it back in. The GPS and the host computer share the same serial port on the AVR, so they will conflict when used together.

Hardware
========

The [Trackuino shield](https://github.com/trackuino/shield) repository contains the Eagle schematic / pcb files of a shield you can build as-is (gerber files are included) or modify to suit your needs. Check its README for details.

Related projects
================

Some other HAB-related projects I wrote:

  * https://github.com/trackuino/hab-tracker - balloon trajectory prediction tool for Android 
  * https://github.com/trackuino/aprsdb - an efficient and queriable APRS database server (required by the Hab Tracker Android app)
  * https://github.com/trackuino/chdk-intervalometer - a LUA intervalometer for the old Canon A570IS camera (which might work on other CHDK cameras too)

Support
=======

Discuss firmware bugs or suggestions in the issue tracker, or ask for help at the [SparkFun Forums](https://forum.sparkfun.com/).

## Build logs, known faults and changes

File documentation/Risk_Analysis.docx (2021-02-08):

- Risk: Lens fogs up/ices up
  - Mitigation: do not use cover outside of lens with sealed cover like GoPro cover
- Risk: Payload lands in tree
  - Mitigation: develop parachute drop mechanism with hot wire or servo retracted pin
- Risk: Balloon pops early
  - Mitigation: determine proper inflation pressure of balloon
  - Mitigation: use gloves at all times when handling balloon to prevent skin oils from contacting it (may not be necessary, check other sources)
  - Mitigation: perform balloon inflation on clean tarp to prevent popping during inflation due to ground texture
  - Mitigation: store balloon before use in dark, dry place at room temperature
- Risk: Primary GPS tracking system (SPOT) loses signal
  - Mitigation: use internal passive gimbal to force vertical orientation of GPS
  - Mitigation: use a redundant GPS system communicating via RF
- Risk: Temperatures are too low for payload electronics
  - Mitigation: use light weight Styrofoam cooler filled with hand warmers
  - Mitigation: perform static test of internal and external temperature during cold night or in freezer to ensure within range of electronics specified ratings
- Risk: Bad weather, high cloud coverage
  - Mitigation: Check weather forecast 3 days in advance and day of planned flight for low wind gusts and low cloud coverage
- Risk: Parachute failure
  - Mitigation: Tie parachute such that it is always deployed
- Risk: Recovery is impeded by 3rd party individuals
  - Mitigation: write a clear label on exterior of payload indicating the payload is Auburn University’s property, its purpose, and how to return it to the recovery team. Place large Auburn logos on each side to clearly indicate it is a University research payload and not a suspicious package.
- Risk: Balloon collides with aircraft
  - Mitigation: use radar reflector as required by FAA. Paint or tape payload with bright orange for high contrast
  - Mitigation: ensure launch and predicted landing site is decently far from airport
  - Mitigation: use rope that can be cut with 50lbs of force (according to FAA regulation) such that aircraft will not be damaged upon collision

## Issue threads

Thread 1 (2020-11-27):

mpl3115a2 temperature not being reported

mcberry23, 2020-11-27:
Using `sensor.temperature` stalls program

mcberry23, 2020-12-14:
Temperature should be accessed after pressure and altitude.

Closed 2020-12-14.

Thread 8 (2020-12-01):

Provide Pi with proper current on battery power

mcberry23, 2020-12-01:

mcberry23, 2020-12-05:
Fixed with new regulator: https://www.amazon.com/Pololu-Step-Down-Voltage-Regulator-D24V50F5/dp/B01M659ER2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

Closed 2020-12-05.

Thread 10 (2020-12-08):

publish gps messages

mcberry23, 2020-12-08:

mcberry23, 2020-12-14:
Used USB UART on Arduino Nano (old bootloader) without any debug messages.  Arduino has adafruit ultimate gps library parser with all output messages disabled.

Closed 2020-12-14.

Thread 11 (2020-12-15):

IMUs are out of calibration

mcberry23, 2020-12-15:

mcberry23, 2020-12-16:
Look into the following:
https://learn.adafruit.com/adafruit-bno055-absolute-orientation-sensor/device-calibration
https://x-io.co.uk/open-source-imu-and-ahrs-algorithms/

mcberry23, 2021-02-08:
BNO055 will be calibrated right before flight.  Bag will be recording during process to help with calibrating ICM20948 IMU in post processing.

Closed 2021-02-08.

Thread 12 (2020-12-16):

Side cam node is ending early

mcberry23, 2020-12-16:
During low alt test, side cam node ended with an error.  The compression is also very costly.  Research is needed to make this node more efficient and robust.

Some ways to solve this are suggested here: https://answers.ros.org/question/240897/publishing-compressed-images-directly-for-120fps-streaming/

Specifically, the format of the image might be changed to MJPG for "Publishing compressed images directly": http://wiki.ros.org/compressed_image_transport

mcberry23, 2021-01-23:
Recording and compressing images from 2 cameras simultaneously uses too much CPU usage.

Closed 2021-01-23.

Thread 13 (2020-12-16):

Test cutdown system

mcberry23, 2020-12-16:
Suspend payload 1ft off ground.  Use ground Arduino transmitter to send command wirelessly to engage relay and heat up nichrome wire.

mcberry23, 2021-01-23:
Completed power supply test.  Now need to integrate with Arduino.

mcberry23, 2021-02-01:
Cutdown system removed from full flight system to reduce risk of premature cutdown.

Closed 2021-02-01.

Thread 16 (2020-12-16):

Run overnight test

mcberry23, 2020-12-16:
Seal box while providing external power and place outside.  Run full_flight.launch and record_no-cam.sh over night.  Process results with ROS bag parser.

mcberry23, 2020-12-19:
Started test at about 10pm and ended at about 7am the next day.  External temperature reached just below freezing.  The internal temperature dropped and then leveled out.  Adding heat with chemical hand-warmers might be necessary.

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

Closed 2020-12-19.

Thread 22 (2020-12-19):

ICM IMU temperature is inconsistent

mcberry23, 2020-12-19:

mcberry23, 2021-01-31:
Switched to adafruit library (https://github.com/adafruit/Adafruit_ICM20X) which does not access registers for temperature.  This is not a critical measurement since the BNO055 IMU does measure temperature.

Closed 2021-01-31.

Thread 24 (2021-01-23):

Add Pi Zero for recording data from side_cam

mcberry23, 2021-01-23:
Recording and compressing images from 2 cameras simultaneously uses too much CPU usage.  A raspberry Pi zero might be able to handle the side camera alone and record a separate bag file.

mcberry23, 2021-02-01:
Created quick script here: https://github.com/mcberry23/simple-usbcam-timelapse

Closed 2021-02-01.

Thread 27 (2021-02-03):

Add Secondary GPS module

mcberry23, 2021-02-03:
Raspberry Pi and Arduino are not capable of sharing the same UART GPS module.  A new one has been purchased and will need to be integrated: https://www.amazon.com/gp/product/B01D1D0F5M/ref=ppx_yo_dt_b_asin_title_o00_s00?ie=UTF8&psc=1

mcberry23, 2021-02-05:
New GPS added and now messages can be received by ROS and Trackduino simultaneously.

Closed 2021-02-05.

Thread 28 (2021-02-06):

BNO055 Clock stretching causing issues

mcberry23, 2021-02-06:
There is an issue where the BNO055 is shutting the i2c bus down due to clock stretching.  The Raspberry Pi is not compatible with clock stretching.  The possible solutions to this problem are:

- Decrease Pi i2c clock speed
- Replace BNO055 with another IMU
- Put BNO055 on dedicated microcontroller and send data to Pi over uart

mcberry23, 2021-02-06:
More workarounds: http://www.advamation.com/knowhow/raspberrypi/rpi-i2c-bug.html
Pull-up fix: https://learn.adafruit.com/adafruit-bno055-absolute-orientation-sensor/faqs
Use UART (pg.33): https://cdn-learn.adafruit.com/downloads/pdf/adafruit-bno055-absolute-orientation-sensor.pdf
https://cdn-learn.adafruit.com/downloads/pdf/bno055-absolute-orientation-sensor-with-raspberry-pi-and-beaglebone-black.pdf

mcberry23, 2021-02-08:
Swapped to UART: https://github.com/GAVLab/bosch_imu_driver

Now working more consistently.

Closed 2021-02-08.

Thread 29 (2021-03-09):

MPL3115a2 still having temperature issues

mcberry23, 2021-03-09:

Closed 2021-04-25.

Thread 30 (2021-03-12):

Camera module

tania-19, 2021-03-12:
Hi!, i am trying to use the raspberry pi camera module V2, i have raspberry pi 4B and ros noetic.

I followed the steps from Set Up Cameras, but when i write rqt_image_view, it seems i cant connect to my camera:
![image](https://user-images.githubusercontent.com/65095904/110992422-a8f43400-8354-11eb-8c89-bbb534e9ba47.png
thanks

tania-19, 2021-03-29:
Hi! I end up using the newest Ubiquity Robotics Image [here](https://downloads.ubiquityrobotics.com/pi.html) the camera module works fine now, but i haven't try this project because it was developed on ros noetic and ubuntu mate 20.04 and now i have ros kinetic.

Closed 2021-04-01.

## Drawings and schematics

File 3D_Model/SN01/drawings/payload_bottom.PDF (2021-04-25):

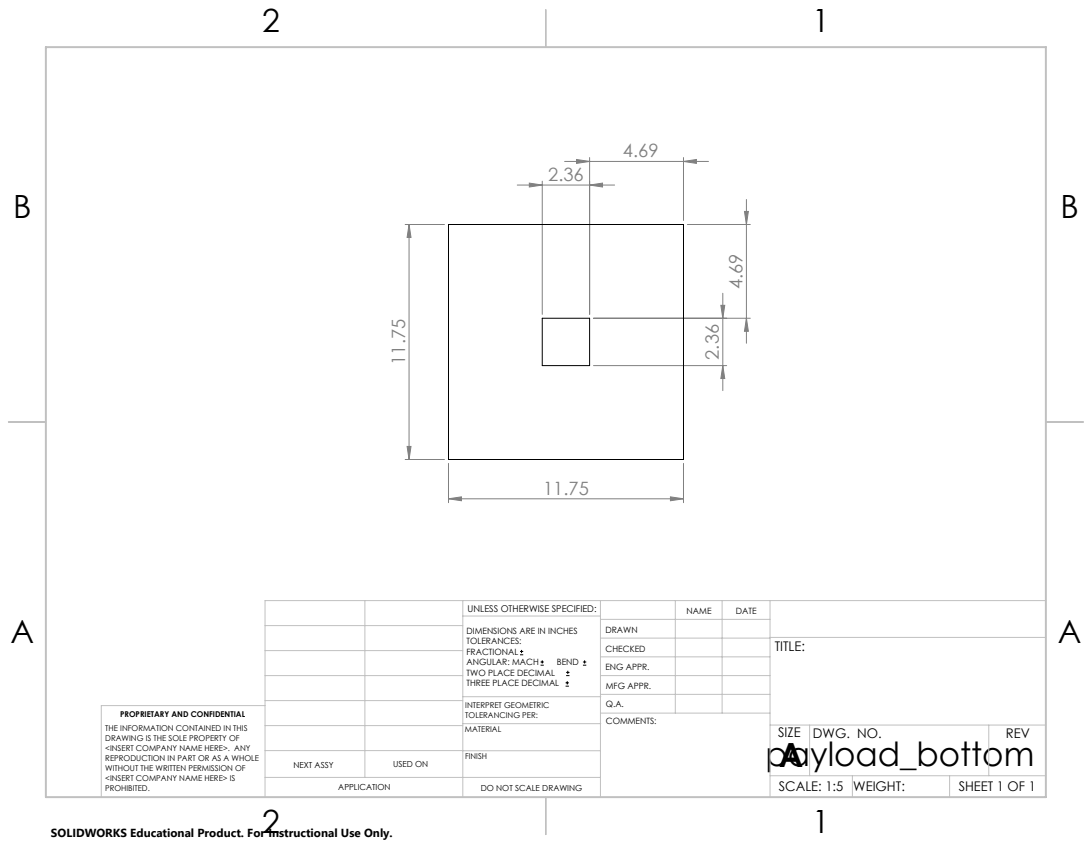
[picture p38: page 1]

UNLESS OTHERWISE SPECIFIED: | | NAME | DATE
DIMENSIONS ARE IN INCHES TOLERANCES: FRACTIONAL ANGULAR: MACH BEND TWO PLACE DECIMAL THREE PLACE DECIMAL | DRAWN

CHECKED | | | TITLE:

ENG APPR.
MFG APPR.

INTERPRET GEOMETRIC TOLERANCING PER: | Q.A.
MATERIAL | payload_bottom | SIZE A | DWG. NO. | REV

PROPRIETARY AND CONFIDENTIAL
THE INFORMATION CONTAINED IN THIS
DRAWING IS THE SOLE PROPERTY OF
<INSERT COMPANY NAME HERE>. ANY
REPRODUCTION IN PART OR AS A WHOLE
WITHOUT THE WRITTEN PERMISSION OF
<INSERT COMPANY NAME HERE> IS
PROHIBITED.

NEXT ASSY | USED ON | FINISH

APPLICATION | DO NOT SCALE DRAWING | | SCALE: 1:5 | WEIGHT: | SHEET 1 OF 1

SOLIDWORKS Educational Product. For Instructional Use Only.

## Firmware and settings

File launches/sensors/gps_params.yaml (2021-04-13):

debug: 1                    # Range 0-4 (0 means no debug statements will print)


device: /dev/ttyUSB0
frame_id: gps
rate: 4                     # in Hz
nav_rate: 4                 # [# of measurement cycles], recommended 1 Hz, may 
                            # be either 5 Hz (Dual constellation) or 
                            # 8 Hz (GPS only)
dynamic_model: airborne4   # Airborne < 4G, 2D fix not supported (3D only), 
                            # Max Alt: 50km
                            # Max Horizontal Velocity: 250 m/s, 
                            # Max Vertical Velocity: 100 m/s
fix_mode: auto

dr_limit: 0

uart1:
  baudrate: 9600 
  in: 1
  out: 1          

gnss:
  glonass: true             # Supported by C94-M8P
  beidou: false             # Supported by C94-M8P
  qzss: false               # Supported by C94-M8P
  galileo: false


dgnss_mode: 3               # Fixed mode

inf: 
  all: true                   # Whether to display all INF messages in console

# Enable u-blox message publishers
publish:
  all: true
  aid:
    hui: false
  nav:
    posecef: false

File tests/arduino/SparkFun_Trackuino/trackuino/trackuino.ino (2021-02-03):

/* trackuino copyright (C) 2010  EA5HAV Javi
 *
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
 * You should have received a copy of the GNU General Public License
 * along with this program; if not, write to the Free Software
 * Foundation, Inc., 51 Franklin Street, Fifth Floor, Boston, MA  02110-1301, USA.
 */

// Mpide 22 fails to compile Arduino code because it stupidly defines ARDUINO 
// as an empty macro (hence the +0 hack). UNO32 builds are fine. Just use the
// real Arduino IDE for Arduino builds. Optionally complain to the Mpide
// authors to fix the broken macro.
#if (ARDUINO + 0) == 0
#error "Oops! We need the real Arduino IDE (version 22 or 23) for Arduino builds."
#error "See trackuino.pde for details on this"

// Refuse to compile on arduino version 21 or lower. 22 includes an 
// optimization of the USART code that is critical for real-time operation
// of the AVR code.
#elif (ARDUINO + 0) < 22
#error "Oops! We need Arduino 22 or 23"
#error "See trackuino.pde for details on this"

#endif


// Trackuino custom libs
#include "config.h"
#include "afsk_avr.h"
#include "afsk_pic32.h"
#include "aprs.h"
#include "buzzer.h"
#include "gps.h"
#include "pin.h"
#include "power.h"
#include "sensors_avr.h"
#include "sensors_pic32.h"
#include <SoftwareSerial.h>

// Arduino/AVR libs
#if (ARDUINO + 1) >= 100
#  include <Arduino.h>
#else
#  include <WProgram.h>
#endif

// Module constants
static const uint32_t VALID_POS_TIMEOUT = 2000;  // ms

// Module variables
static int32_t next_aprs = 0;


void setup()
{
  pinMode(LED_PIN, OUTPUT);
  pin_write(LED_PIN, LOW);

  Serial.begin(GPS_BAUDRATE);
#ifdef DEBUG_RESET
  Serial.println("RESET");
#endif

  buzzer_setup();
  afsk_setup();
  gps_setup();
  sensors_setup();

#ifdef DEBUG_SENS
  Serial.print("Ti=");
  Serial.print(sensors_int_lm60());
  Serial.print(", Te=");
  Serial.print(sensors_ext_lm60());
  Serial.print(", Vin=");
  Serial.println(sensors_vin());
#endif

  // Do not start until we get a valid time reference
  // for slotted transmissions.
  if (APRS_SLOT >= 0) {
    do {
      while (! Serial.available())
        power_save();
    } while (! gps_decode(Serial.read()));
    
    next_aprs = millis() + 1000 *
      (APRS_PERIOD - (gps_seconds + APRS_PERIOD - APRS_SLOT) % APRS_PERIOD);
  }
  else {
    next_aprs = millis();
  }  
  // TODO: beep while we get a fix, maybe indicating the number of
  // visible satellites by a series of short beeps?
}

void get_pos()
{
  // Get a valid position from the GPS
  int valid_pos = 0;
  uint32_t timeout = millis();

#ifdef DEBUG_GPS
  Serial.println("\nget_pos()");
#endif

  gps_reset_parser();

  do {
    if (Serial.available())
      valid_pos = gps_decode(Serial.read());
  } while ( (millis() - timeout < VALID_POS_TIMEOUT) && ! valid_pos) ;

  if (valid_pos) {
    if (gps_altitude > BUZZER_ALTITUDE) {
      buzzer_off();   // In space, no one can hear you buzz
    } else {
      buzzer_on();
    }
  }
}

void loop()
{
  // Time for another APRS frame
  if ((int32_t) (millis() - next_aprs) >= 0) {
    get_pos();
    aprs_send();
    next_aprs += APRS_PERIOD * 1000L;
    while (afsk_flush()) {
      power_save();
    }

#ifdef DEBUG_MODEM
    // Show modem ISR stats from the previous transmission
    afsk_debug();
#endif

  } else {
    // Discard GPS data received during sleep window
    while (Serial.available()) {
      Serial.read();
    }
  }

  power_save(); // Incoming GPS data or interrupts will wake us up
}

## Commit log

2020-11-17 Added more documents and updated readme.
    [bom.xlsx]
2020-11-19 Updated readme installation instructions
    [bom.xlsx]
2020-11-19 Added code for imu and alt sensor
2020-11-26 Added ROS project with IMU integration. Altimeter project is not operational yet
2020-11-26 Added imu submodule
2020-11-26 Replaced url for imu
2020-11-28 Added camera nodes
    [bom.xlsx]
2020-12-01 Added ground station code
    [bom.xlsx]
2020-12-07 Recent updates
    [bom.xlsx]
2020-12-07 Added test script for second imu
2020-12-07 Added icm20948 imu ros package
2020-12-08 Calibrated cameras. Needs redone with correct block size
2020-12-09 Added correct camera calibrations
    [GPS_Parsing.ino, HelloWorld.ino, gps_simpletest.py]
2020-12-09 Added ros bag recording and fixed calibration of bottom camera
2020-12-13 Fixed camera compression issue. Recalibrated down cam
2020-12-14 Added GPS ros driver
2020-12-15 Added IMU and raspicam_node. Various launch file and documentation improvements
2020-12-17 Added air pressure calculations documentation
2021-01-28 Created ros-imu-bno055 calibration script
2021-01-30 Improving data output during calibration
2021-02-01 Updated checklist
    [flight_path_2-2-21.csv]
2021-02-02 Added script to view all sensors status at once
2021-02-07 Changed BNO055 from i2c to UART
2021-02-07 Changed calibration bash script naming
2021-02-13 Added more documentation about the first flight.
    [bom.xlsx, flight_path.csv, predicted_flight_path.csv]
2021-02-26 Documentation improvements
    [bom.xlsx]
2021-03-31 Improved launch files. Added working GPS and power monitor nodes.
2021-04-09 Fully integrated ros arduino ins
2021-04-09 Added transforms for IMUs
2021-04-13 Added Flight 2 information.
    [bom.xlsx, stratotrack_data.csv]
2021-04-23 Minor path changes
    [bom.xlsx]
2021-04-25 More minor updates
    [bom.xlsx]
2021-04-25 Added more photos and 3D models.
    [12pin-header.SLDPRT, 12pin-header.stp, 1_5V_holder4AA.x_t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]

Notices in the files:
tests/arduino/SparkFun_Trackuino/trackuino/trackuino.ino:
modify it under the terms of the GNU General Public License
